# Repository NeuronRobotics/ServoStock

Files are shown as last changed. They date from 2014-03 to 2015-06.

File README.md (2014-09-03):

ServoStock
==========

This is the repository for the bowler enabled, closed loop controlled 3d printer. This repository is for all of the code for the printer.

# Control Application

From Eclipse for Java

* https://github.com/NeuronRobotics/java-bowler
* https://github.com/NeuronRobotics/NrConsole
* Jmonkey Game Engine

# Dependancies

## Compiler and c-bowler
Clone the c-bowler repository and install the compilers from here:

* https://github.com/NeuronRobotics/c-bowler

##MPLabx

Install MPLABX from here:

http://www.microchip.com/pagehandler/en-us/family/mplabx/

# Opening projects

Both repositoried should be in the same folder on your disk.

Open c-bowler in MPLABX

```
c-bowler/firmware/library/NR-Clib/development/c-bowler.X
```

And the ServoStock Code

```
ServoStock/firmware/MplabX_Projects/ServoPrinterController.X
```

You are ready to build and program.

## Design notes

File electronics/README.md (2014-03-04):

These are the assembly instructions for the ServoStock Electronics platform

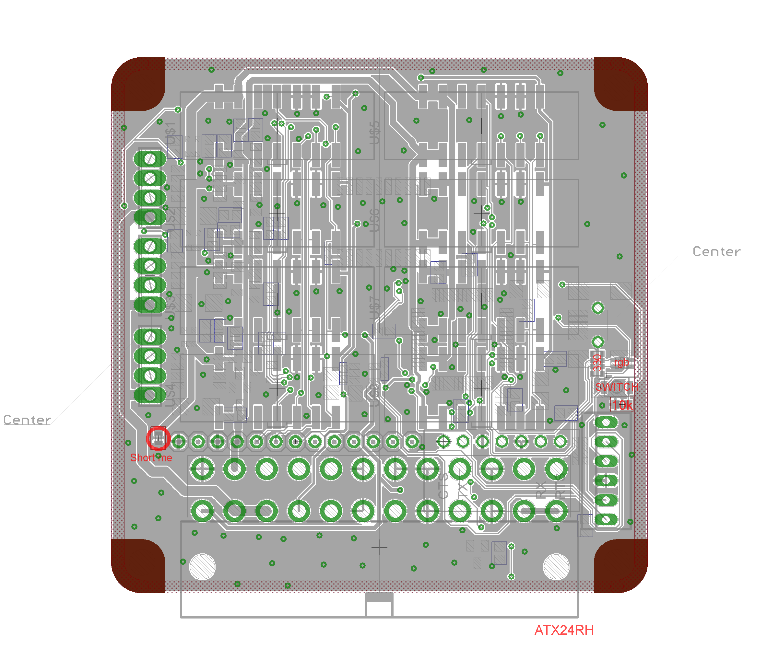
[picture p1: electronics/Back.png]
Top Components

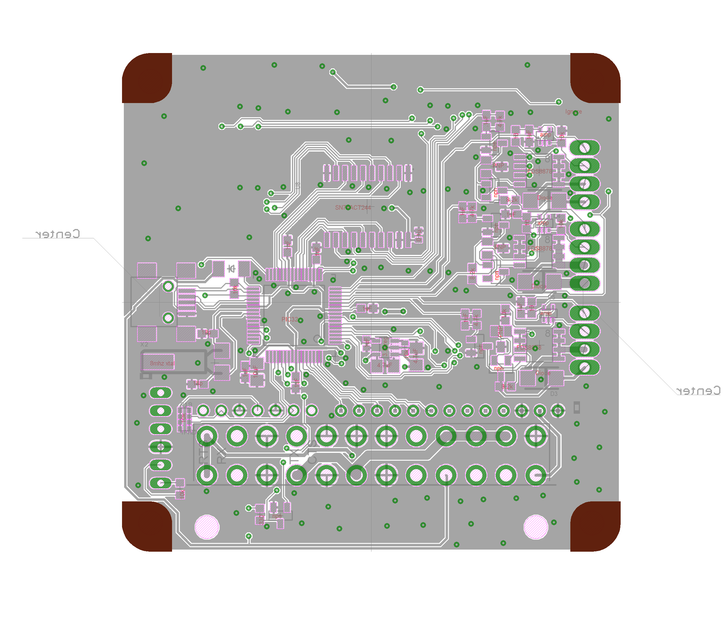
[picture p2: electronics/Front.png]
Bottom Components


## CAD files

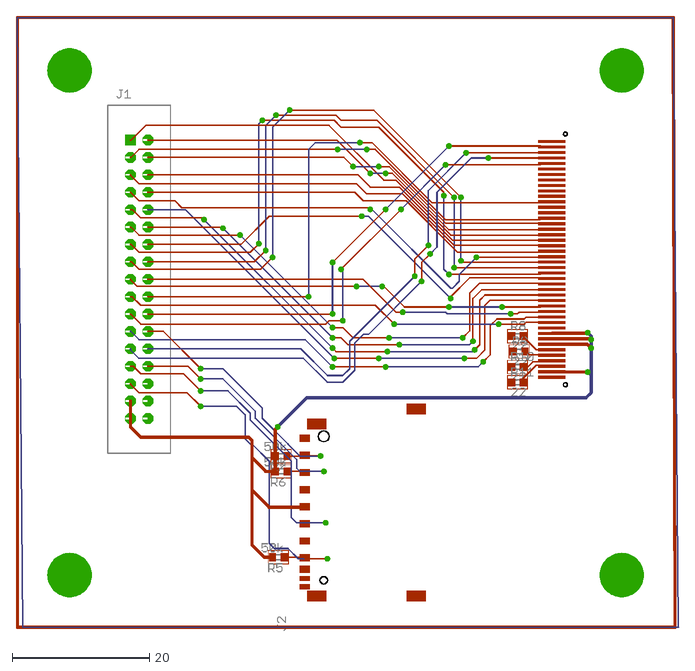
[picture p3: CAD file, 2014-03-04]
electronics/ReplicatorElectronics/lcd_brd/lcd_brd.dxf
96.8 x 89.7

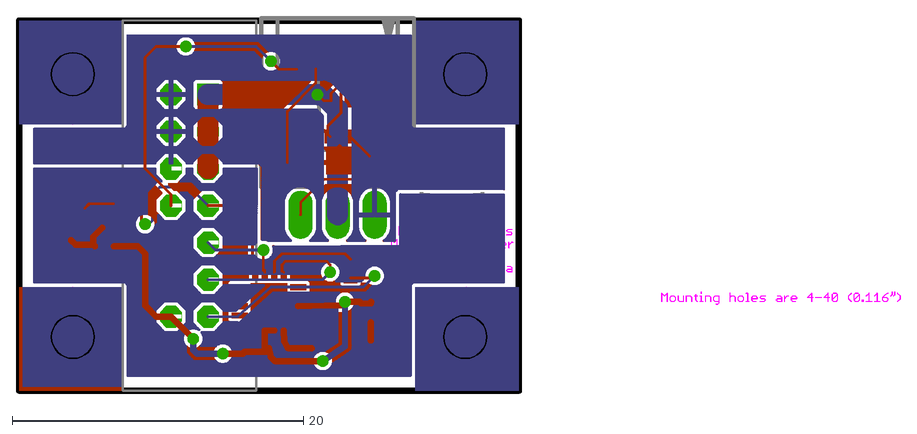
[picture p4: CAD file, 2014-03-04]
electronics/ReplicatorElectronics/magencoder/MagEnc2.dxf
60.7 x 25.9

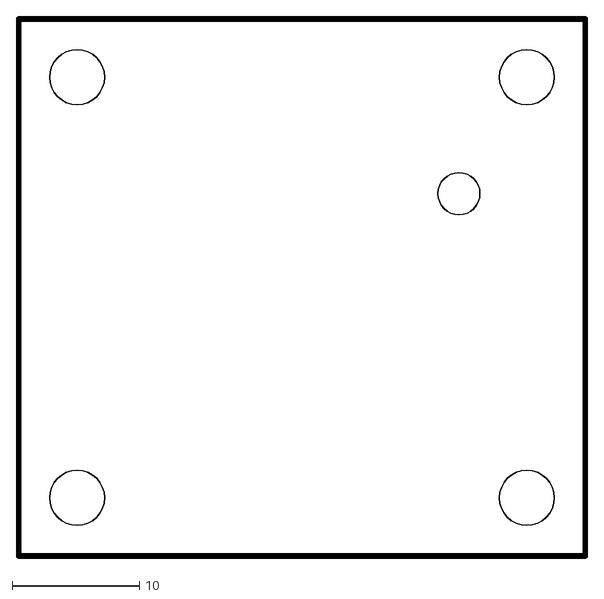
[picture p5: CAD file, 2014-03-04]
electronics/ReplicatorElectronics/temp_control/temp_control_holes.dxf
44.9 x 42.6

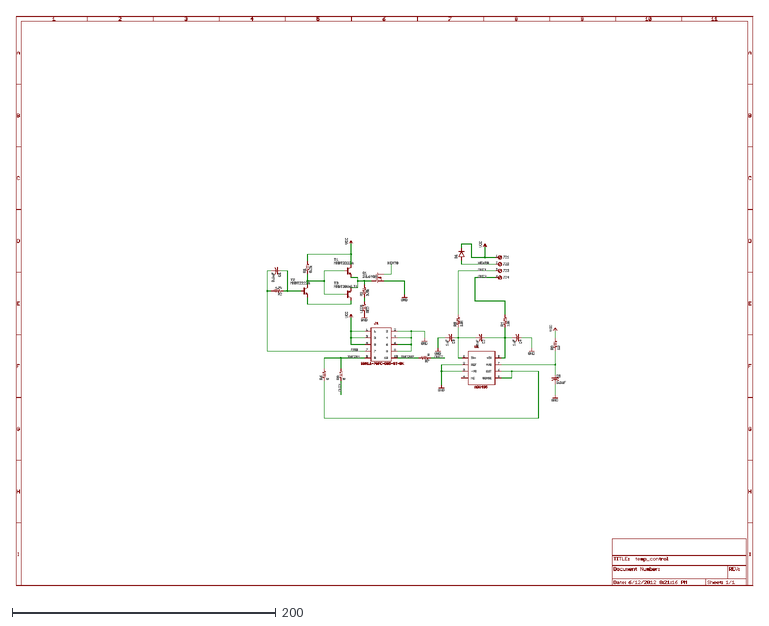
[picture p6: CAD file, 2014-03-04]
electronics/ReplicatorElectronics/temp_control/temp_control.dxf
559.1 x 432.1

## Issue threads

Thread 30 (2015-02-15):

Make a test Jig for an axis

acamilo, 2015-02-15:
Test jig needs to contain an aligned encoder board, motor, and magnet and needs to not become a part of another robot.

madhephaestus, 2015-02-16:
The spring-pin board needs to be created so these can be checked as fast as checking the dyio. Once the spring pin board is created, assign it to kent to build the jig.

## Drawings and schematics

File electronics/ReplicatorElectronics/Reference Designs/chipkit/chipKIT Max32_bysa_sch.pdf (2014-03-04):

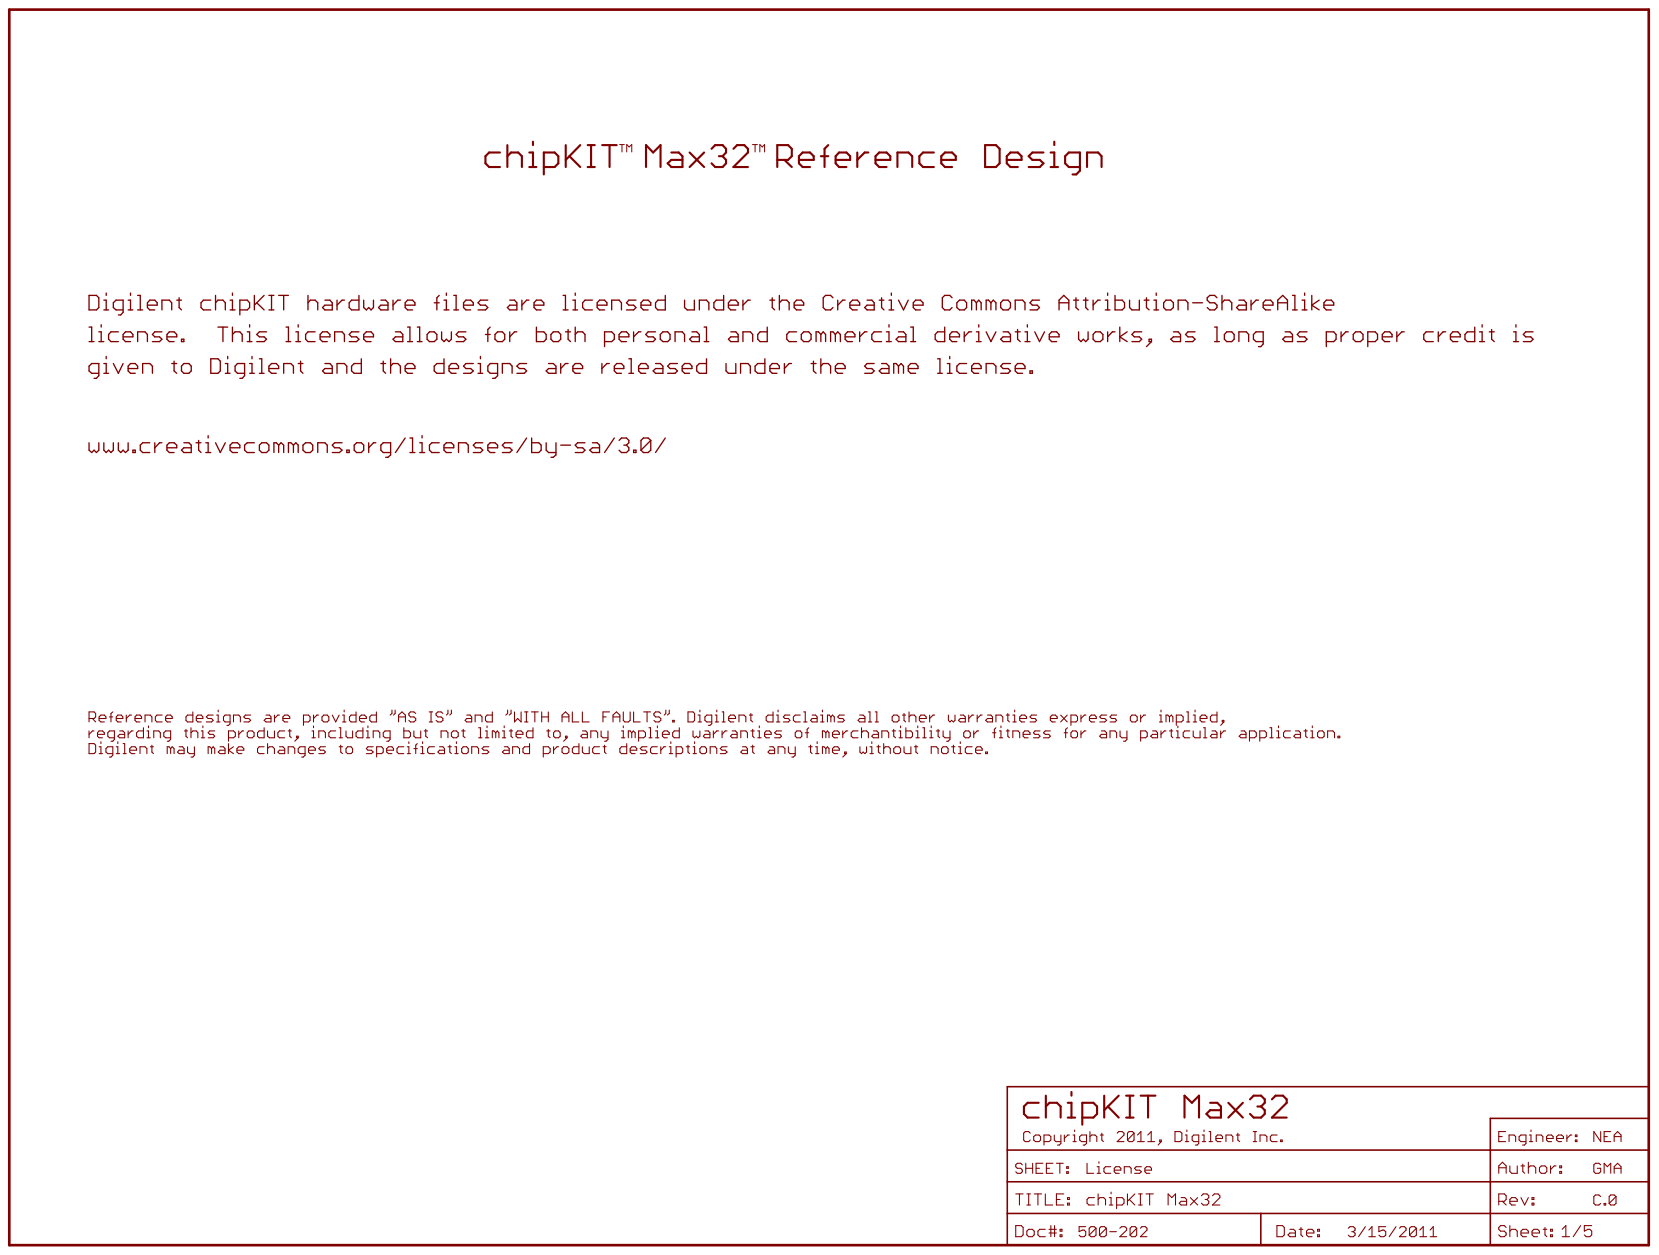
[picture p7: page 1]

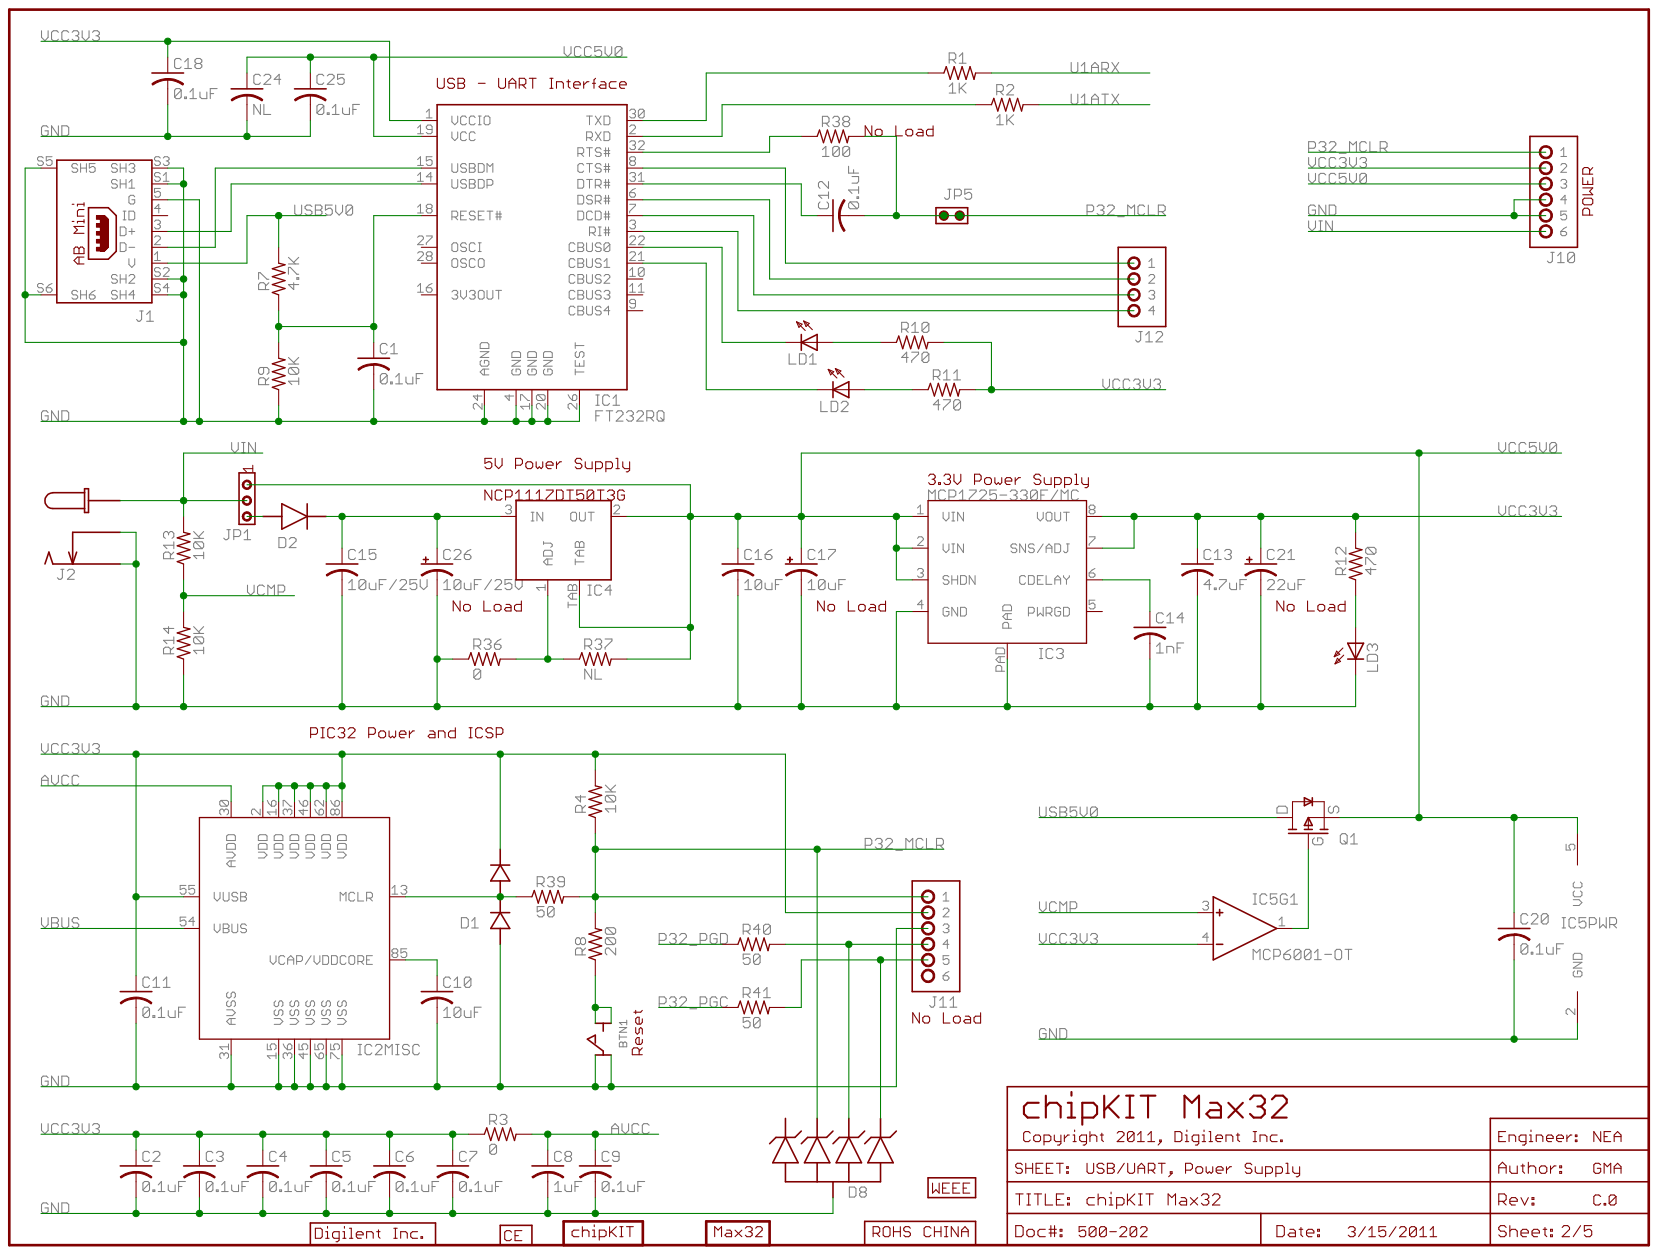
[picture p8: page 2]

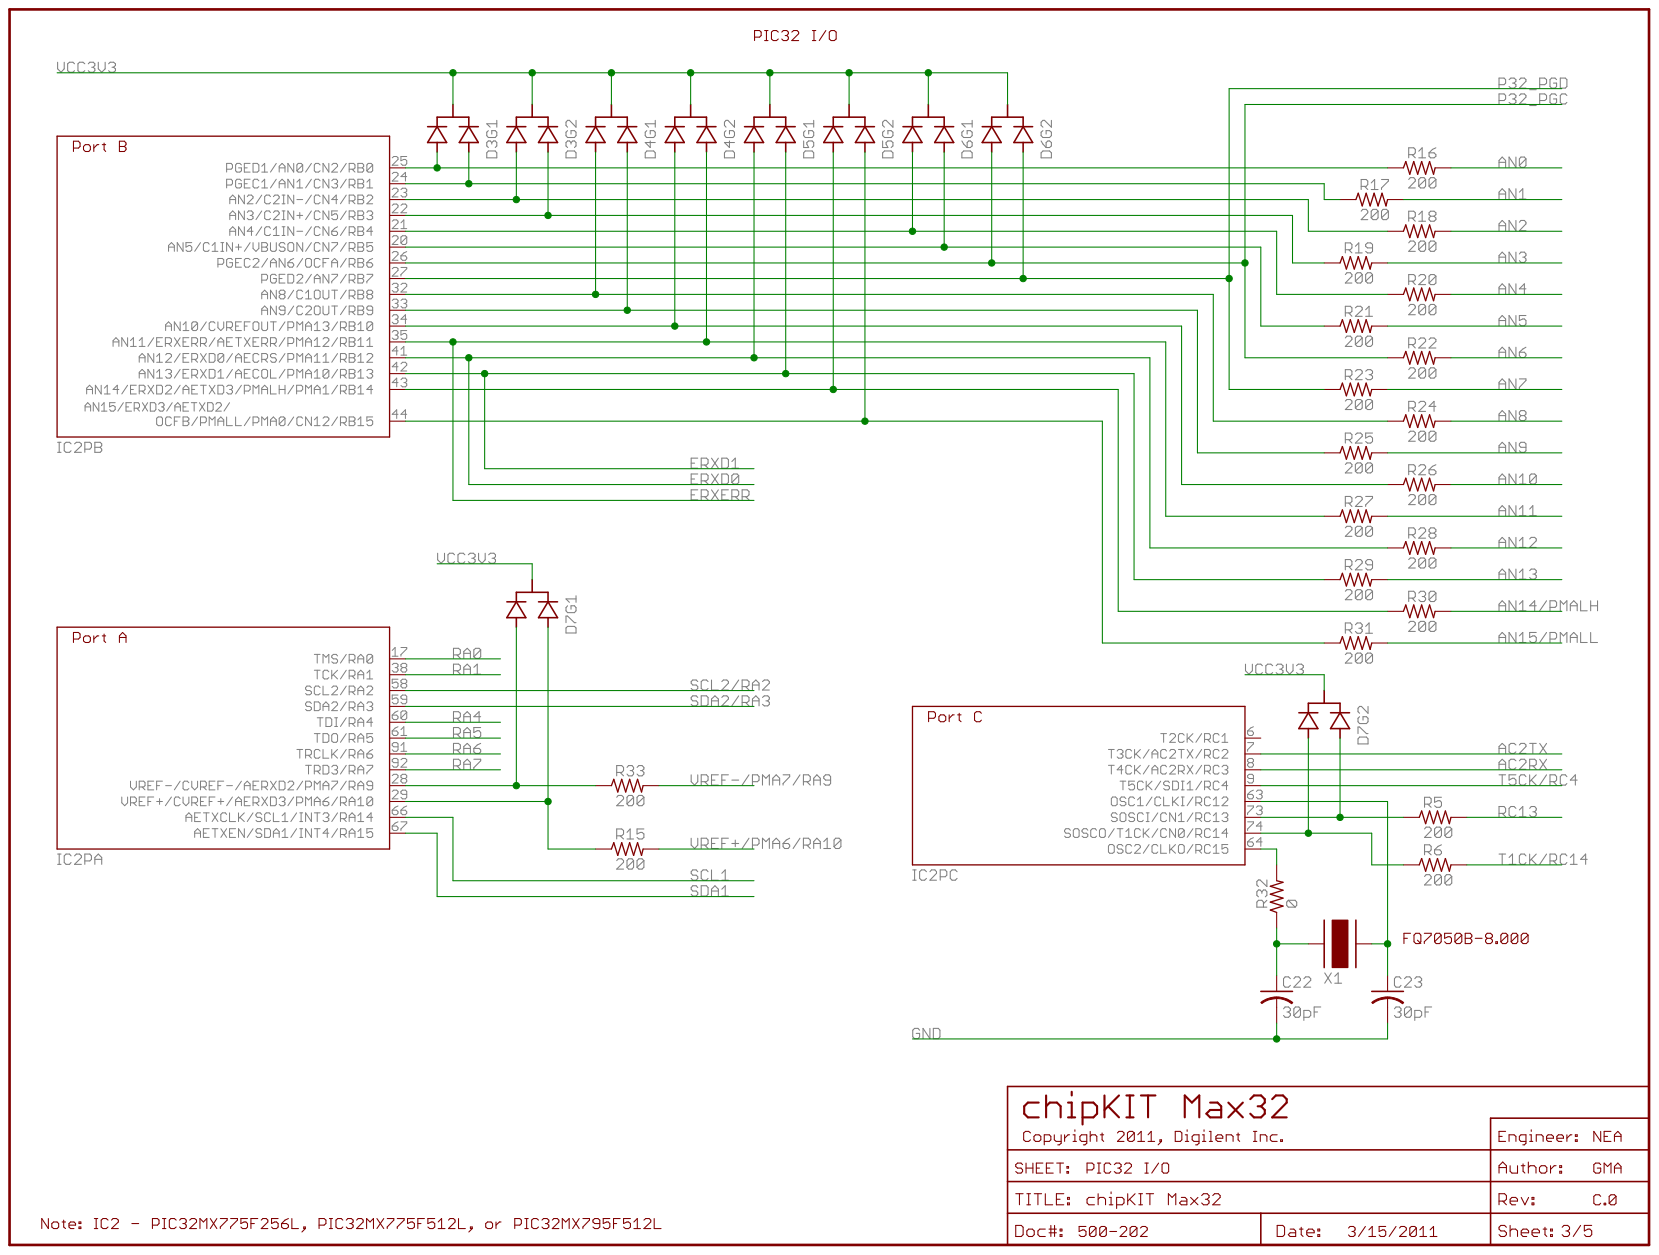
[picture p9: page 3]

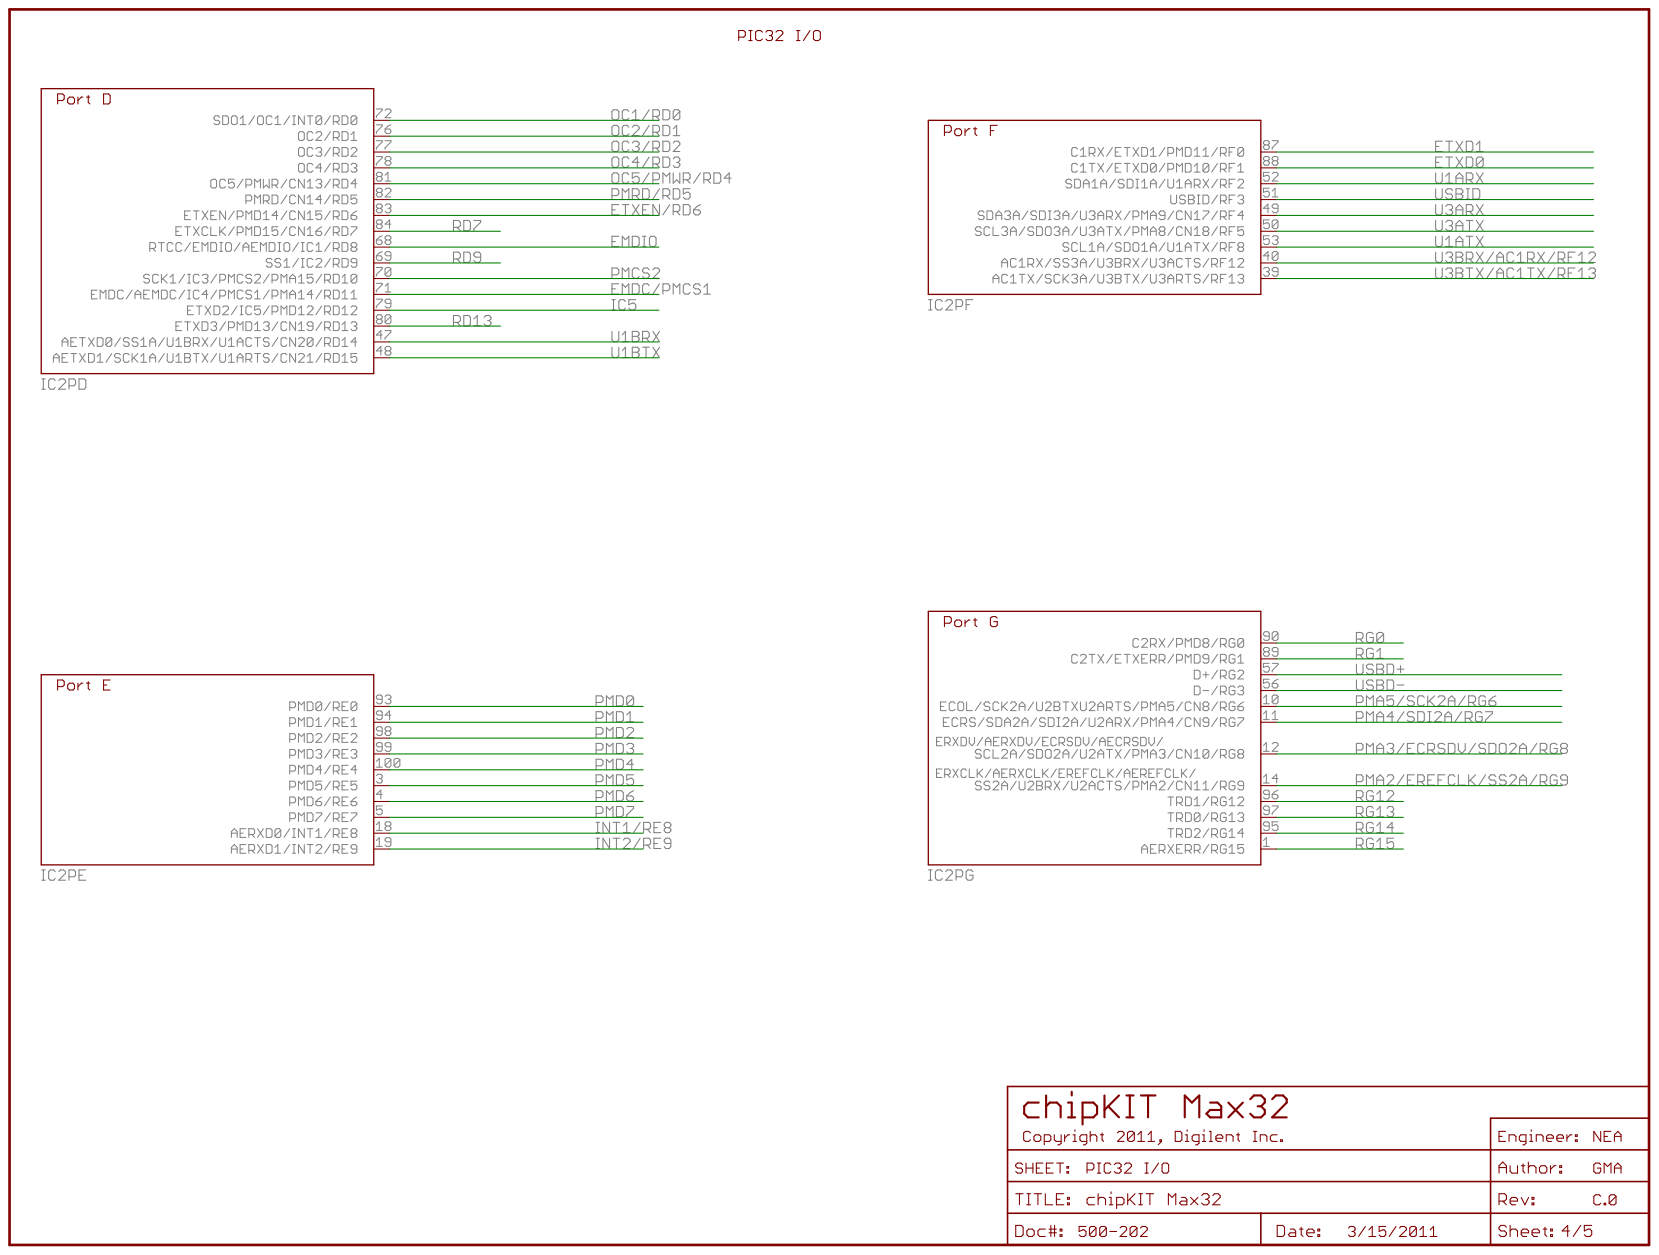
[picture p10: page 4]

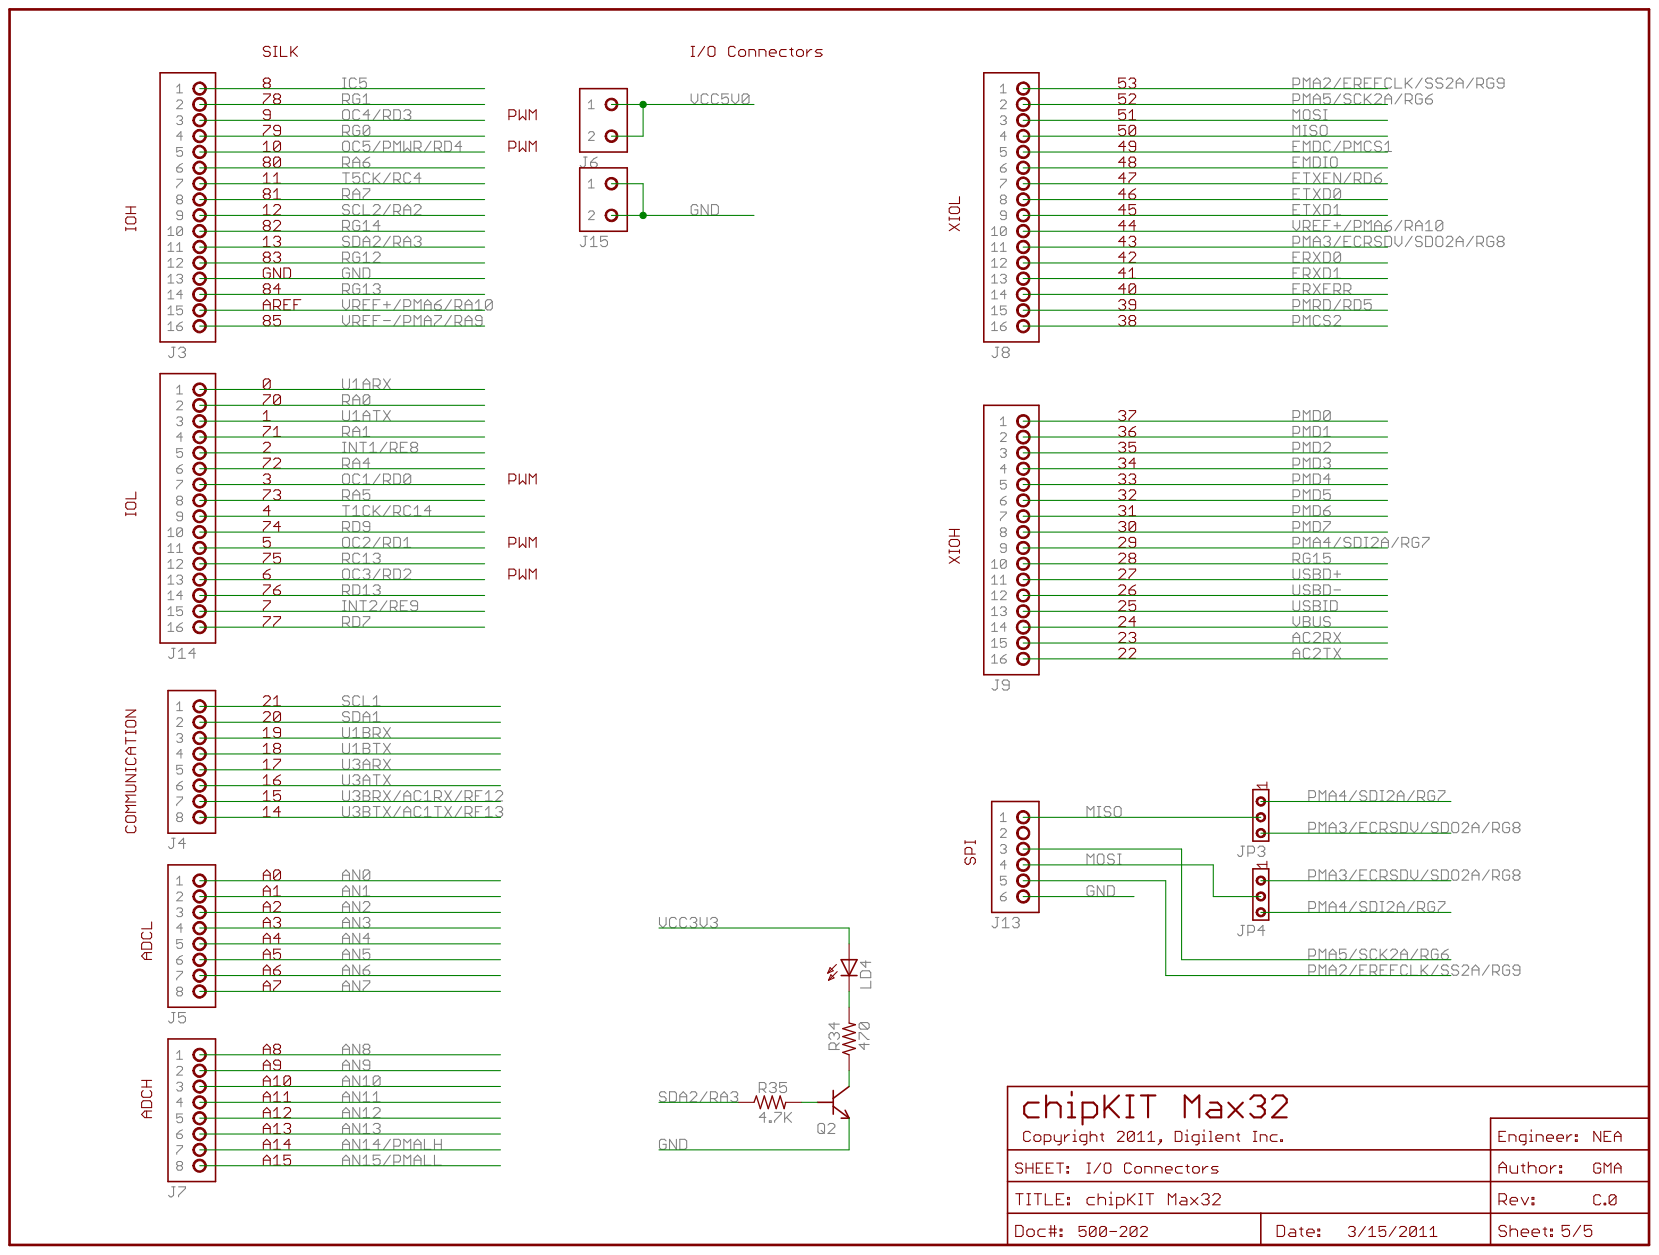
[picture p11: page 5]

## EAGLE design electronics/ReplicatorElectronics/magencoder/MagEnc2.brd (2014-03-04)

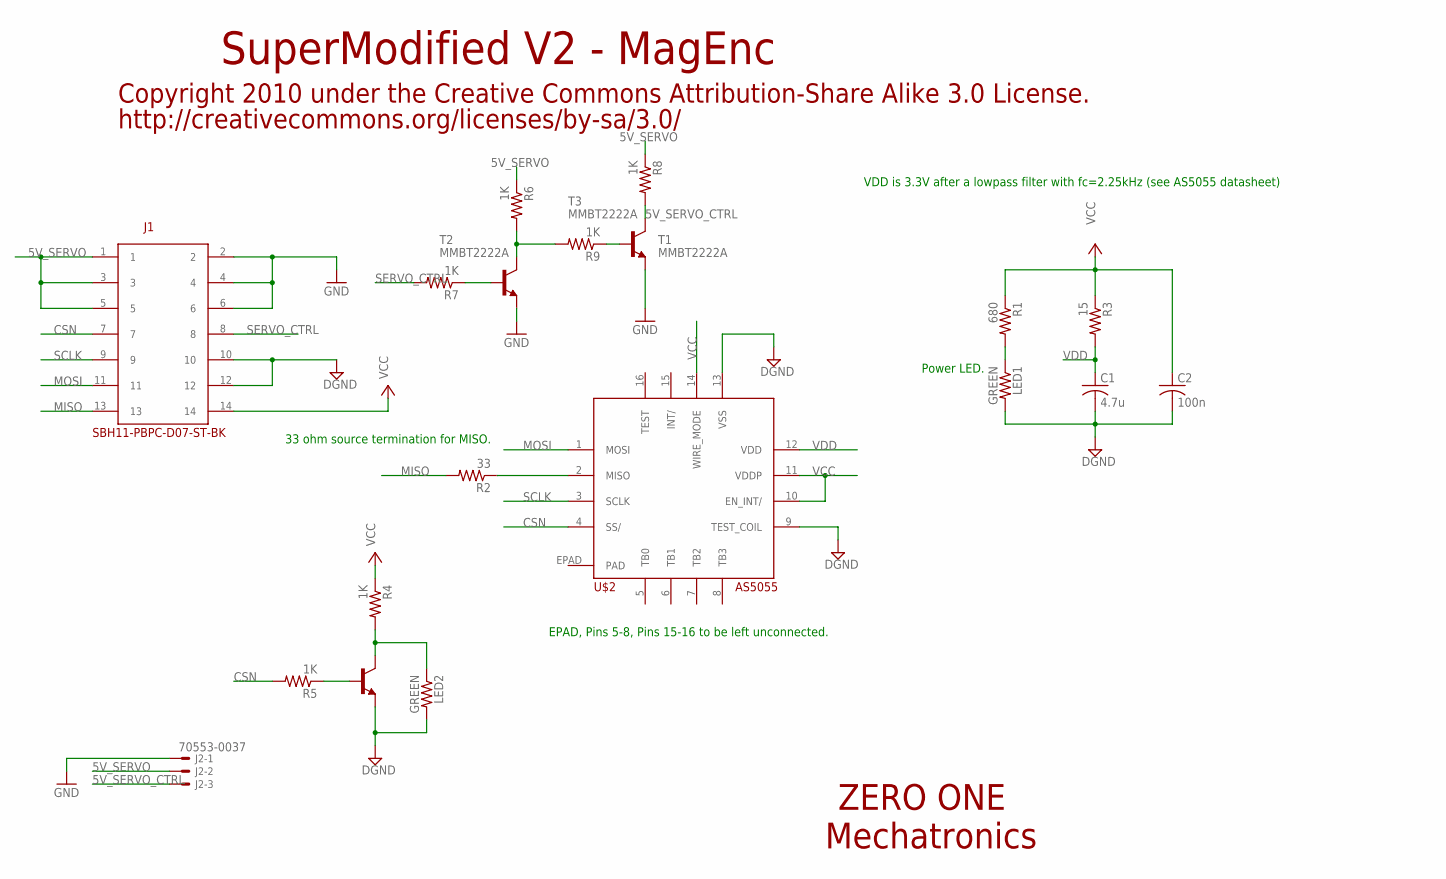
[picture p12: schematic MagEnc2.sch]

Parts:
C1: 4.7u; C0402
C2: 100n; C0402
J1: SBH11-PBPC-D07-ST-BK
J2: 70553-0037; 70553-03
LED1, LED2: GREEN; R0402
R1: 680; R0402
R2: 33; R0402
R3: 15; R0402
R4, R5, R6, R7, R8, R9: 1K; R0402
T1, T2, T3: MMBT2222A; SOT23-BEC
U$2: AS5055

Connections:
5V_SERVO: J1.1, J1.3, J1.5, J2.2, R6.1, R8.1
5V_SERVO_CTRL: J2.3, R8.2, T3.C
CSN: J1.7, R5.2, U$2.4 (SS/)
CSN1: R6.2, R9.2, T2.C
DGND: C1.2, C2.2, J1.10, J1.12, LED1.2, LED2.2, T1.E, U$2.9 (TEST_COIL), U$2.13 (VSS)
GND: J1.2, J1.4, J1.6, J2.1, T2.E, T3.E
MISO: J1.13, R2.2
MOSI: J1.11, U$2.1 (MOSI)
unnamed: LED1.1, R1.2
unnamed: LED2.1, R4.2, T1.C
unnamed: R5.1, T1.B
unnamed: R2.1, U$2.2 (MISO)
unnamed: R7.1, T2.B
unnamed: R9.1, T3.B
SCLK: J1.9, U$2.3 (SCLK)
SERVO_CTRL: J1.8, R7.2
VCC: C2.1, J1.14, R1.1, R3.1, R4.1, U$2.10 (EN_INT/), U$2.11 (VDDP), U$2.14 (WIRE_MODE)
VDD: C1.1, R3.2, U$2.12 (VDD)

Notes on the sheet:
ZERO ONE
Mechatronics
SuperModified V2 - MagEnc
Copyright 2010 under the Creative Commons Attribution-Share Alike 3.0 License.
http://creativecommons.org/licenses/by-sa/3.0/
VDD is 3.3V after a lowpass filter with fc=2.25kHz (see AS5055 datasheet)
EPAD, Pins 5-8, Pins 15-16 to be left unconnected.
33 ohm source termination for MISO.
Power LED.

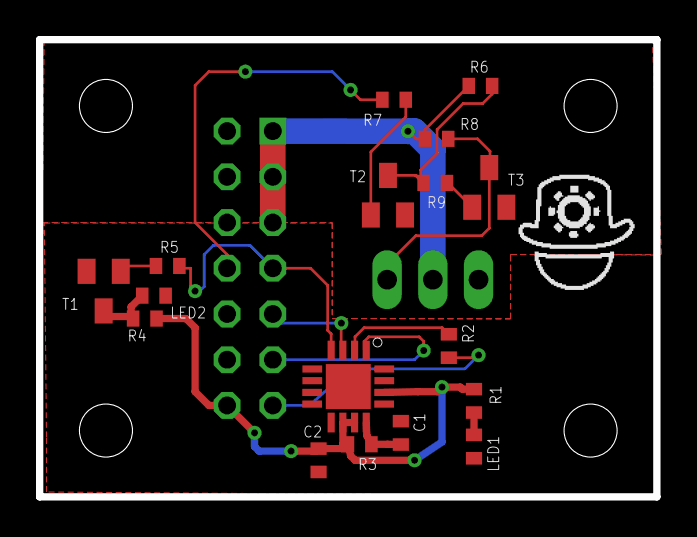
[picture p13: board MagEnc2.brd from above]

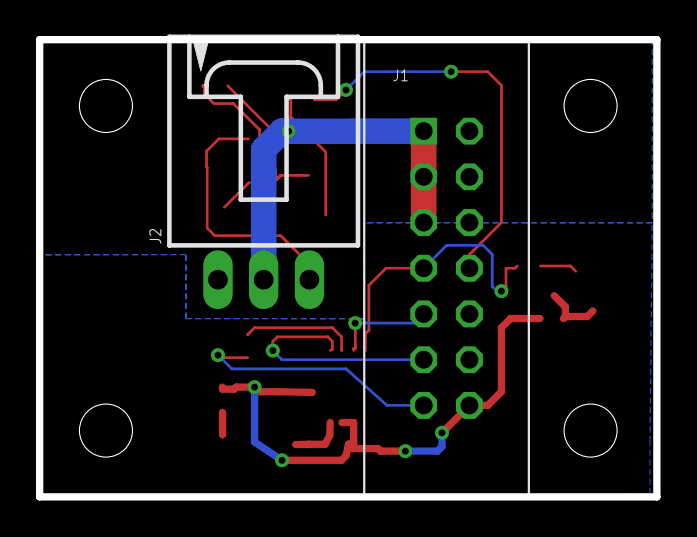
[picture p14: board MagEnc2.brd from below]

Board: 2 copper layers, 34.3 x 25.4 mm, 19 parts (2 on the bottom side), 18 nets.

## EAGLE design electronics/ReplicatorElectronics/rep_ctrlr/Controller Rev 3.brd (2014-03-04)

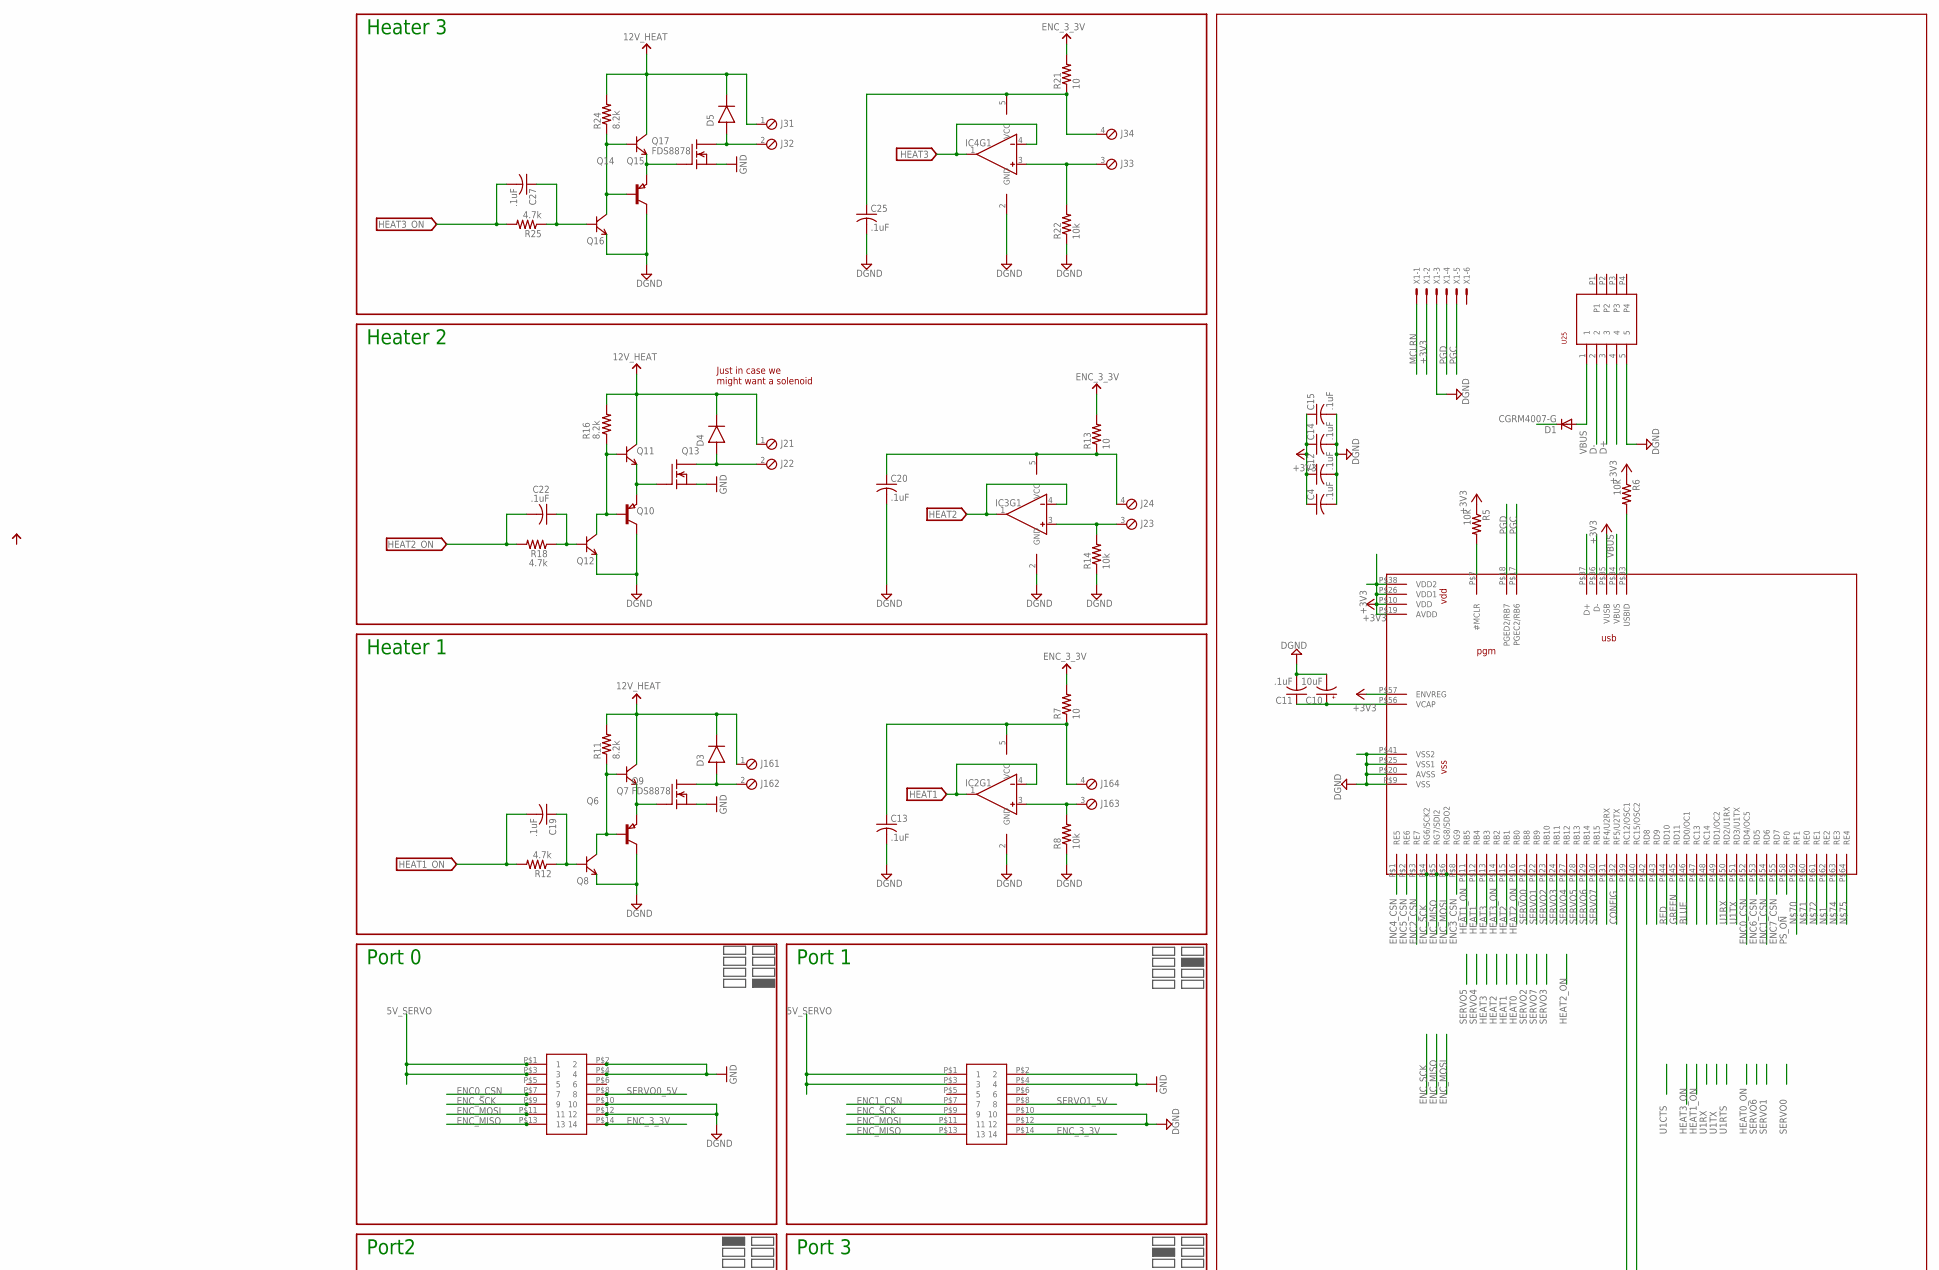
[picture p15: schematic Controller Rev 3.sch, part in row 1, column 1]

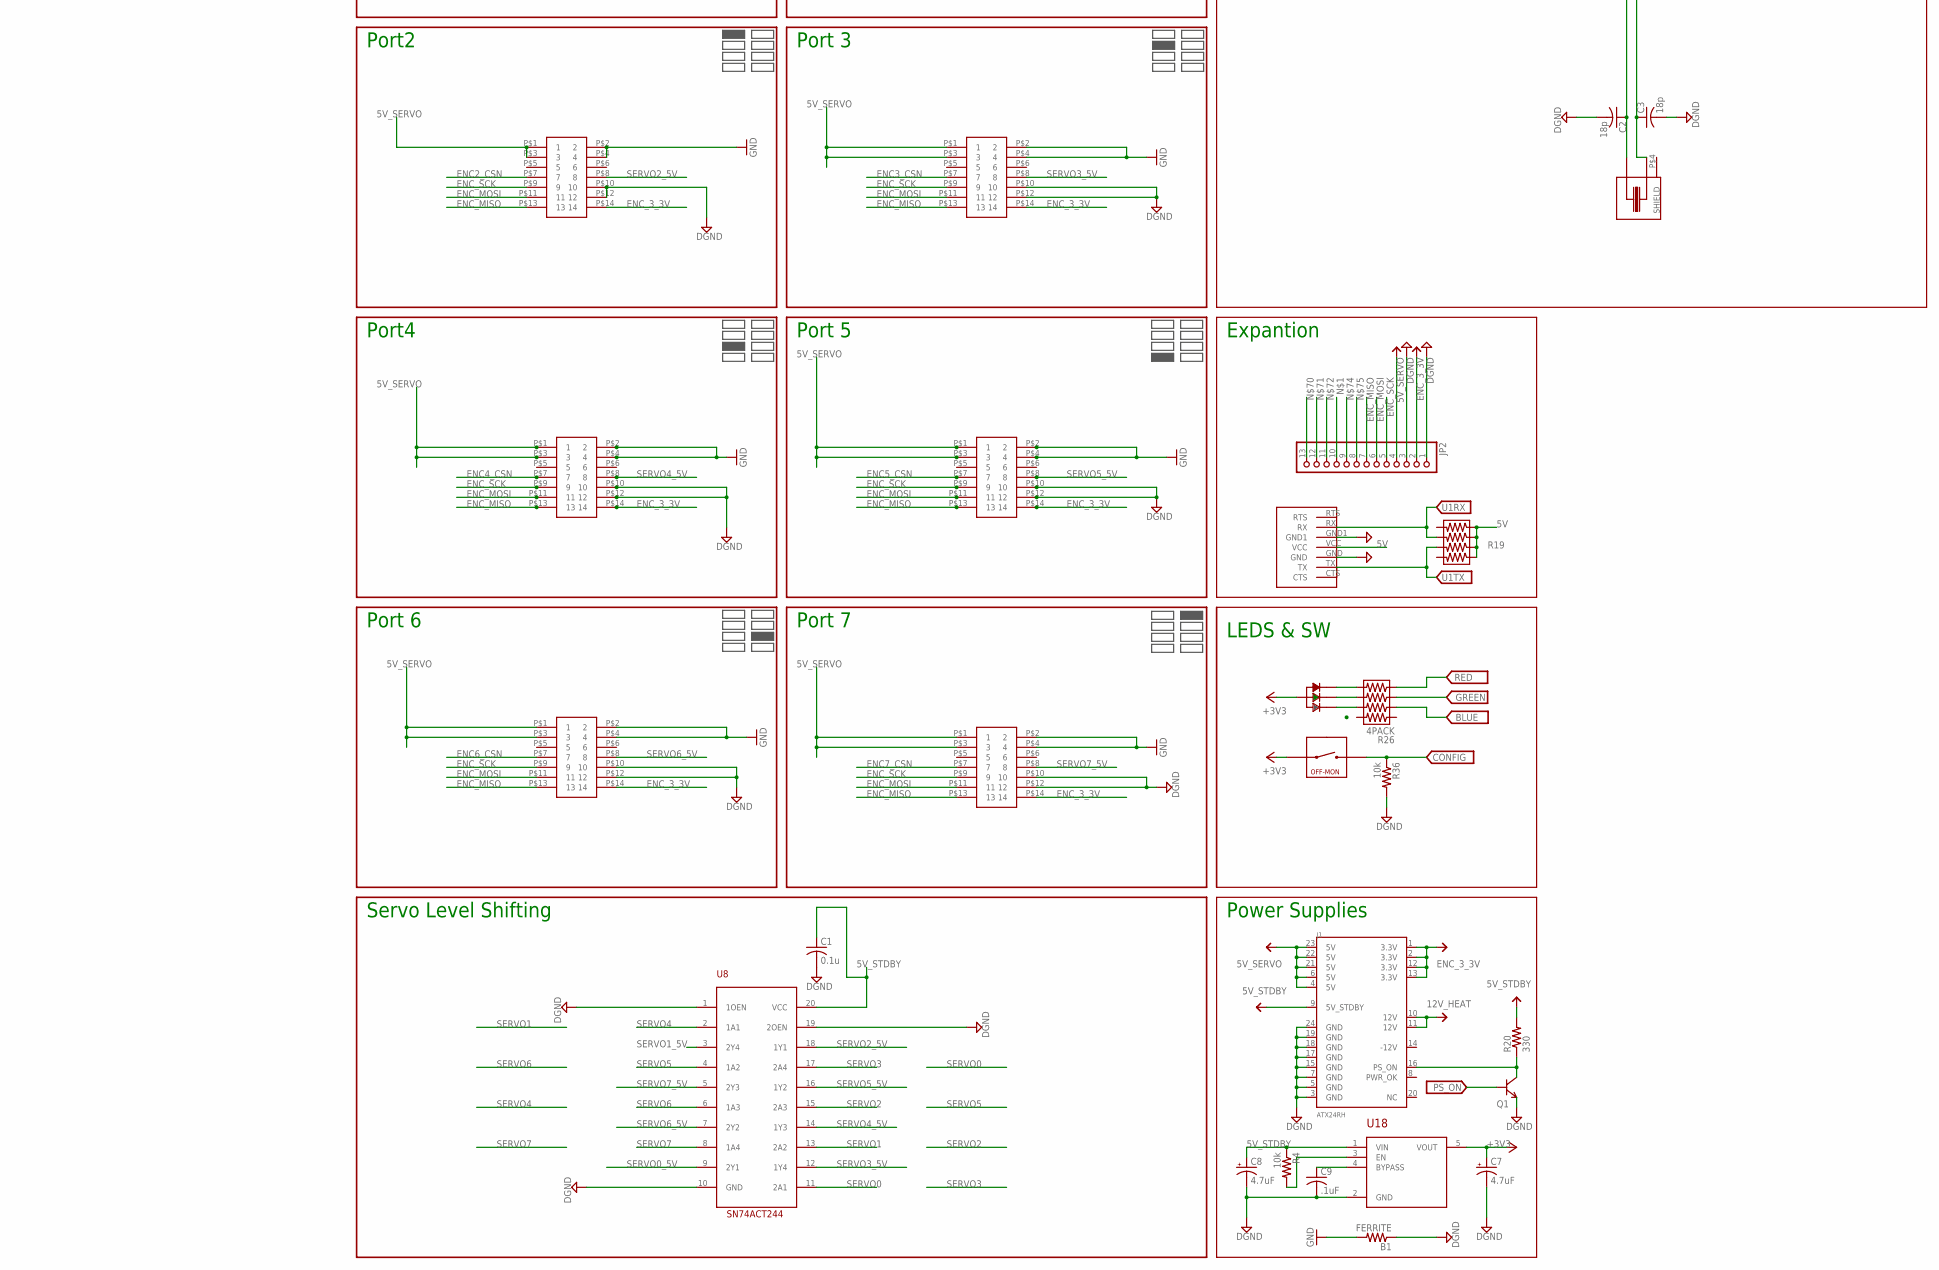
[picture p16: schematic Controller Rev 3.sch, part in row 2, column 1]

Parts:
B1: FERRITE; R0603
C1: 0.1u; C0402
C2, C3: 18p; C0603
C4, C11, C12, C13, C14, C15, C19, C20, C22, C25, C27: .1uF; C0603
C7, C8: 4.7uF; R/2012-12R
C9: .1uF; C0402
C10: 10uF; R/2012-12R
D1: CGRM4007-G; SOD-123_MINI-SMA
D3, D4, D5: DISCRETE_DIODESMA; DISCRETE_SMA
IC2, IC3, IC4: MICROCHIP_MCP6001-LT; MICROCHIP_SC70-5-LT
J1: ATX24RH; ATX24_RIGHT_ANGLE
J2, J3, J16: OSTVN04A150; 4POL254
J10: WASP7PIN
JP2: PINHD-1X13_BIG; 1X13-BIG
Q1, Q7, Q8, Q11, Q12, Q15, Q16: DISCRETE_MMBT3904LT1G; DISCRETE_SOT23
Q6, Q10, Q14: PNP-TRANSISTOR_SOT23; SOT23
Q9, Q13, Q17: FDS8878; SO-8
R4: 10k; R0402
R5, R6, R8, R14, R22, R36: 10k; R0603
R7, R13, R21: 10; R0603
R11, R16, R24: 8.2k; R0603
R12, R18, R25: 4.7k; R0603
R19, R26: 4PACK; 4PACK_0603
R20: 330; R0603
SW3: SPST; B3U-1000P
U1: TRI-LED-SMD; TRI_LED_SMD
U3: PIC32-64TQFP64-2; TQFP64-2
U8: SN74ACT244; 20-SOIC
U18: LDS3985XX33; SOT23-5
U25: 1734035-1_USB; 1734035-1_1734035
U$1, U$2, U$3, U$4, U$5, U$6, U$7, U$8: SBH11-NBPC-D07-SM-BK
X1: 22-23-2061
X2: CMR3XXT; CMR309T

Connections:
5V: J10.VCC, R19.R1B, R19.R2B, R19.R3B, R19.R4B
5V_SERVO: J1.4 (5V), J1.6 (5V), J1.21 (5V), J1.22 (5V), J1.23 (5V), JP2.4, U$1.P$1 (1), U$1.P$3 (3), U$2.P$1 (1), U$2.P$3 (3), U$3.P$1 (1), U$3.P$3 (3), U$4.P$1 (1), U$4.P$3 (3), U$5.P$1 (1), U$5.P$3 (3), U$6.P$1 (1), U$6.P$3 (3), U$7.P$1 (1), U$7.P$3 (3), U$8.P$1 (1), U$8.P$3 (3)
5V_STDBY: C1.1, C8.+, D1.C, J1.9 (5V_STDBY), R4.1, R20.2, U8.20 (VCC), U18.1 (VIN)
12V_HEAT: D3.C, D4.C, D5.C, J1.10 (12V), J1.11 (12V), J2.1, J3.1, J16.1, Q7.3 (C), Q11.3 (C), Q15.3 (C), R11.2, R16.2, R24.2
12V_SW1: D3.A, J16.2, Q9.5 (D), Q9.6 (D), Q9.7 (D), Q9.8 (D)
12V_SW2: D4.A, J2.2, Q13.5 (D), Q13.6 (D), Q13.7 (D), Q13.8 (D)
12V_SW3: D5.A, J3.2, Q17.5 (D), Q17.6 (D), Q17.7 (D), Q17.8 (D)
+3V3: C4.1, C7.+, C12.1, C14.1, C15.1, R5.1, R6.1, SW3.P$1, U1.COMM-A, U3.P$10 (VDD), U3.P$19 (AVDD), U3.P$26 (VDD1), U3.P$35 (VUSB), U3.P$38 (VDD2), U3.P$57 (ENVREG), U18.5 (VOUT), X1.2
B: R26.R2A, U1.BLUE
BLUE: R26.R2B, U3.P$46 (RD0/OC1)
CONFIG: R36.1, SW3.P$3, U3.P$32 (RF5/U2TX)
D+: U3.P$37 (D+), U25.3
D-: U3.P$36 (D-), U25.2
DGND: B1.1, C1.2, C2.2, C3.2, C4.2, C7.-, C8.-, C9.2, C10.-, C11.2, C12.2, C13.2, C14.2, C15.2, C20.2, C25.2, IC2.2 (GND), IC3.2 (GND), IC4.2 (GND), J1.3 (GND), J1.5 (GND), J1.7 (GND), J1.15 (GND), J1.17 (GND), J1.18 (GND), J1.19 (GND), J1.24 (GND), J10.GND, J10.GND1, JP2.1, JP2.3, Q1.2 (E), Q6.3 (C), Q8.2 (E), Q10.3 (C), Q12.2 (E), Q14.3 (C), Q16.2 (E), R8.1, R14.1, R22.1, R36.2, U3.P$9 (VSS), U3.P$20 (AVSS), U3.P$25 (VSS1), U3.P$41 (VSS2), U8.1 (1OEN), U8.10 (GND), U8.19 (2OEN), U18.2 (GND), U25.5, U$1.P$10 (10), U$1.P$12 (12), U$2.P$10 (10), U$2.P$12 (12), U$3.P$10 (10), U$3.P$12 (12), U$4.P$10 (10), U$4.P$12 (12), U$5.P$10 (10), U$5.P$12 (12), U$6.P$10 (10), U$6.P$12 (12), U$7.P$10 (10), U$7.P$12 (12), U$8.P$10 (10), U$8.P$12 (12), X1.3
ENC0_CSN: U3.P$52 (RD4/OC5), U$8.P$7 (7)
ENC1_CSN: U3.P$54 (RD6), U$6.P$7 (7)
ENC2_CSN: U3.P$3 (RE7), U$1.P$7 (7)
ENC3_CSN: U3.P$8 (RG9), U$2.P$7 (7)
ENC4_CSN: U3.P$1 (RE5), U$3.P$7 (7)
ENC5_CSN: U3.P$2 (RE6), U$4.P$7 (7)
ENC6_CSN: U3.P$53 (RD5), U$7.P$7 (7)
ENC7_CSN: U3.P$55 (RD7), U$5.P$7 (7)
ENC_3_3V: J1.1 (3.3V), J1.2 (3.3V), J1.12 (3.3V), J1.13 (3.3V), JP2.2, R7.2, R13.2, R21.2, U$1.P$14 (14), U$2.P$14 (14), U$3.P$14 (14), U$4.P$14 (14), U$5.P$14 (14), U$6.P$14 (14), U$7.P$14 (14), U$8.P$14 (14)
ENC_MISO: JP2.7, U3.P$5 (RG7/SDI2), U$1.P$13 (13), U$2.P$13 (13), U$3.P$13 (13), U$4.P$13 (13), U$5.P$13 (13), U$6.P$13 (13), U$7.P$13 (13), U$8.P$13 (13)
ENC_MOSI: JP2.6, U3.P$6 (RG8/SDO2), U$1.P$11 (11), U$2.P$11 (11), U$3.P$11 (11), U$4.P$11 (11), U$5.P$11 (11), U$6.P$11 (11), U$7.P$11 (11), U$8.P$11 (11)
ENC_SCK: JP2.5, U3.P$4 (RG6/SCK2), U$1.P$9 (9), U$2.P$9 (9), U$3.P$9 (9), U$4.P$9 (9), U$5.P$9 (9), U$6.P$9 (9), U$7.P$9 (9), U$8.P$9 (9)
G: R26.R3A, U1.GRN
GND: B1.2, Q9.1 (S), Q9.2 (S), Q9.3 (S), Q13.1 (S), Q13.2 (S), Q13.3 (S), Q17.1 (S), Q17.2 (S), Q17.3 (S), U$1.P$2 (2), U$1.P$4 (4), U$2.P$2 (2), U$2.P$4 (4), U$3.P$2 (2), U$3.P$4 (4), U$4.P$2 (2), U$4.P$4 (4), U$5.P$2 (2), U$5.P$4 (4), U$6.P$2 (2), U$6.P$4 (4), U$7.P$2 (2), U$7.P$4 (4), U$8.P$2 (2), U$8.P$4 (4)
GREEN: R26.R3B, U3.P$45 (RD11)
HEAT1: IC2.1 (OUT), IC2.4 (IN-), U3.P$12 (RB4)
HEAT1_ON: C19.2, R12.2, U3.P$11 (RB5)
HEAT2: IC3.1 (OUT), IC3.4 (IN-), U3.P$15 (RB1)
HEAT2_ON: C22.2, R18.2, U3.P$16 (RB0)
HEAT3: IC4.1 (OUT), IC4.4 (IN-), U3.P$13 (RB3)
HEAT3_ON: C27.2, R25.2, U3.P$14 (RB2)
MCLRN: R5.2, U3.P$7 (#MCLR), X1.1
unnamed: JP2.10, U3.P$62 (RE2)
unnamed: R4.2, U18.3 (EN)
unnamed: C9.1, U18.4 (BYPASS)
unnamed: C3.1, U3.P$40 (RC15/OSC2), X2.P$3
unnamed: C10.+, C11.1, U3.P$56 (VCAP)
unnamed: C2.1, U3.P$39 (RC12/OSC1), X2.P$1
unnamed: IC2.3 (IN+), J16.3, R8.2
unnamed: C13.1, IC2.5 (VCC), J16.4, R7.1
unnamed: Q6.1 (B), Q7.1 (B), Q8.3 (C), R11.1
unnamed: C19.1, Q8.1 (B), R12.1
unnamed: Q6.2 (E), Q7.2 (E), Q9.4 (G)
unnamed: IC3.3 (IN+), J2.3, R14.2
unnamed: C20.1, IC3.5 (VCC), J2.4, R13.1
unnamed: Q10.1 (B), Q11.1 (B), Q12.3 (C), R16.1
unnamed: C22.1, Q12.1 (B), R18.1
unnamed: Q10.2 (E), Q11.2 (E), Q13.4 (G)
unnamed: IC4.3 (IN+), J3.3, R22.2
unnamed: C25.1, IC4.5 (VCC), J3.4, R21.1
unnamed: Q14.1 (B), Q15.1 (B), Q16.3 (C), R24.1
unnamed: C27.1, Q16.1 (B), R25.1
unnamed: Q14.2 (E), Q15.2 (E), Q17.4 (G)
unnamed: J1.16 (PS_ON), Q1.3 (C), R20.1
unnamed: JP2.13, U3.P$59 (RF1)
unnamed: JP2.12, U3.P$60 (RE0)
unnamed: JP2.11, U3.P$61 (RE1)
unnamed: JP2.9, U3.P$63 (RE3)
unnamed: JP2.8, U3.P$64 (RE4)
PGC: U3.P$17 (PGEC2/RB6), X1.5
PGD: U3.P$18 (PGED2/RB7), X1.4
PS_ON: Q1.1 (B), U3.P$58 (RF0)
R: R26.R4A, U1.RED
RED: R26.R4B, U3.P$44 (RD10)
SERVO0: U3.P$21 (RB8), U8.11 (2A1)
SERVO0_5V: U8.9 (2Y1), U$8.P$8 (8)
SERVO1: U3.P$22 (RB9), U8.13 (2A2)
SERVO1_5V: U8.3 (2Y4), U$6.P$8 (8)
SERVO2: U3.P$23 (RB10), U8.15 (2A3)
SERVO2_5V: U8.18 (1Y1), U$1.P$8 (8)
SERVO3: U3.P$24 (RB11), U8.17 (2A4)
SERVO3_5V: U8.12 (1Y4), U$2.P$8 (8)
SERVO4: U3.P$27 (RB12), U8.2 (1A1)
SERVO4_5V: U8.14 (1Y3), U$3.P$8 (8)
SERVO5: U3.P$28 (RB13), U8.4 (1A2)
SERVO5_5V: U8.16 (1Y2), U$4.P$8 (8)
SERVO6: U3.P$29 (RB14), U8.6 (1A3)
SERVO6_5V: U8.7 (2Y2), U$7.P$8 (8)
SERVO7: U3.P$30 (RB15), U8.8 (1A4)
SERVO7_5V: U8.5 (2Y3), U$5.P$8 (8)
U1RX: J10.RX, R19.R2A, U3.P$50 (RD2/U1RX)
U1TX: J10.TX, R19.R3A, U3.P$51 (RD3/U1TX)
USBID: R6.2, U3.P$33 (USBID), U25.4
VBUS: D1.A, U3.P$34 (VBUS), U25.1

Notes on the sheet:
Just in case we might want a solenoid
Heater 2
Heater 1
Heater 3
LEDS & SW
Power Supplies
Servo Level Shifting
Port 6
Port 7
Port 5
Port4
Port2
Port 3
Port 1
Port 0
Expantion

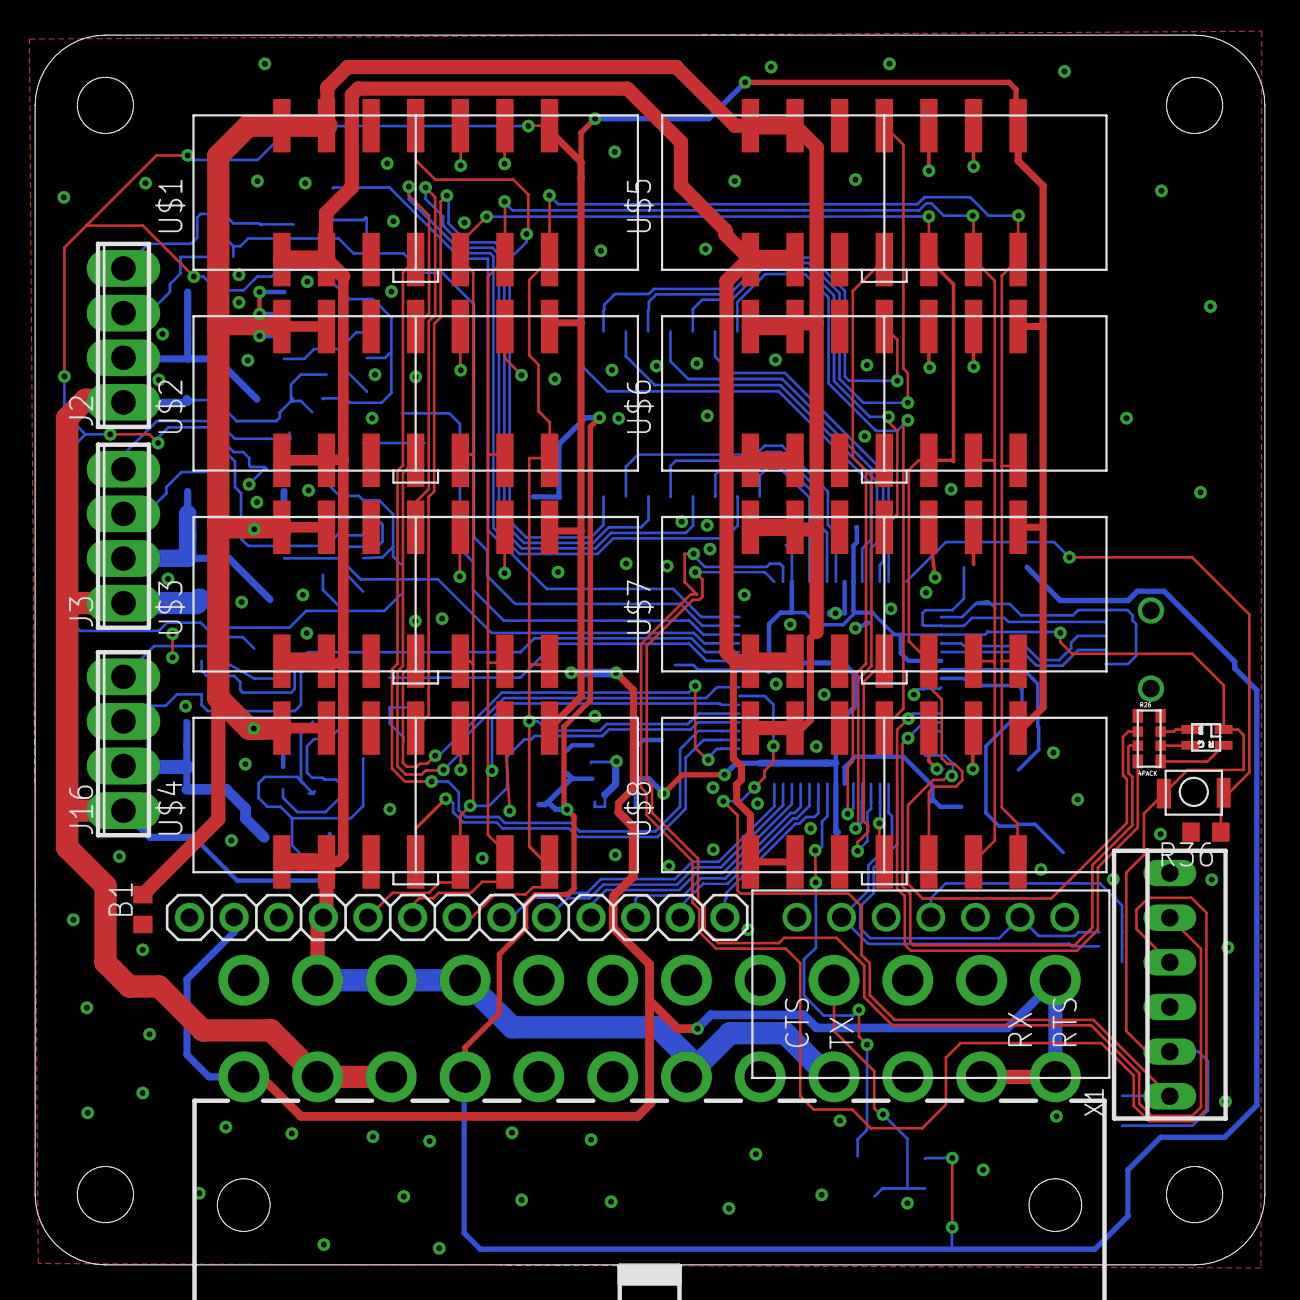
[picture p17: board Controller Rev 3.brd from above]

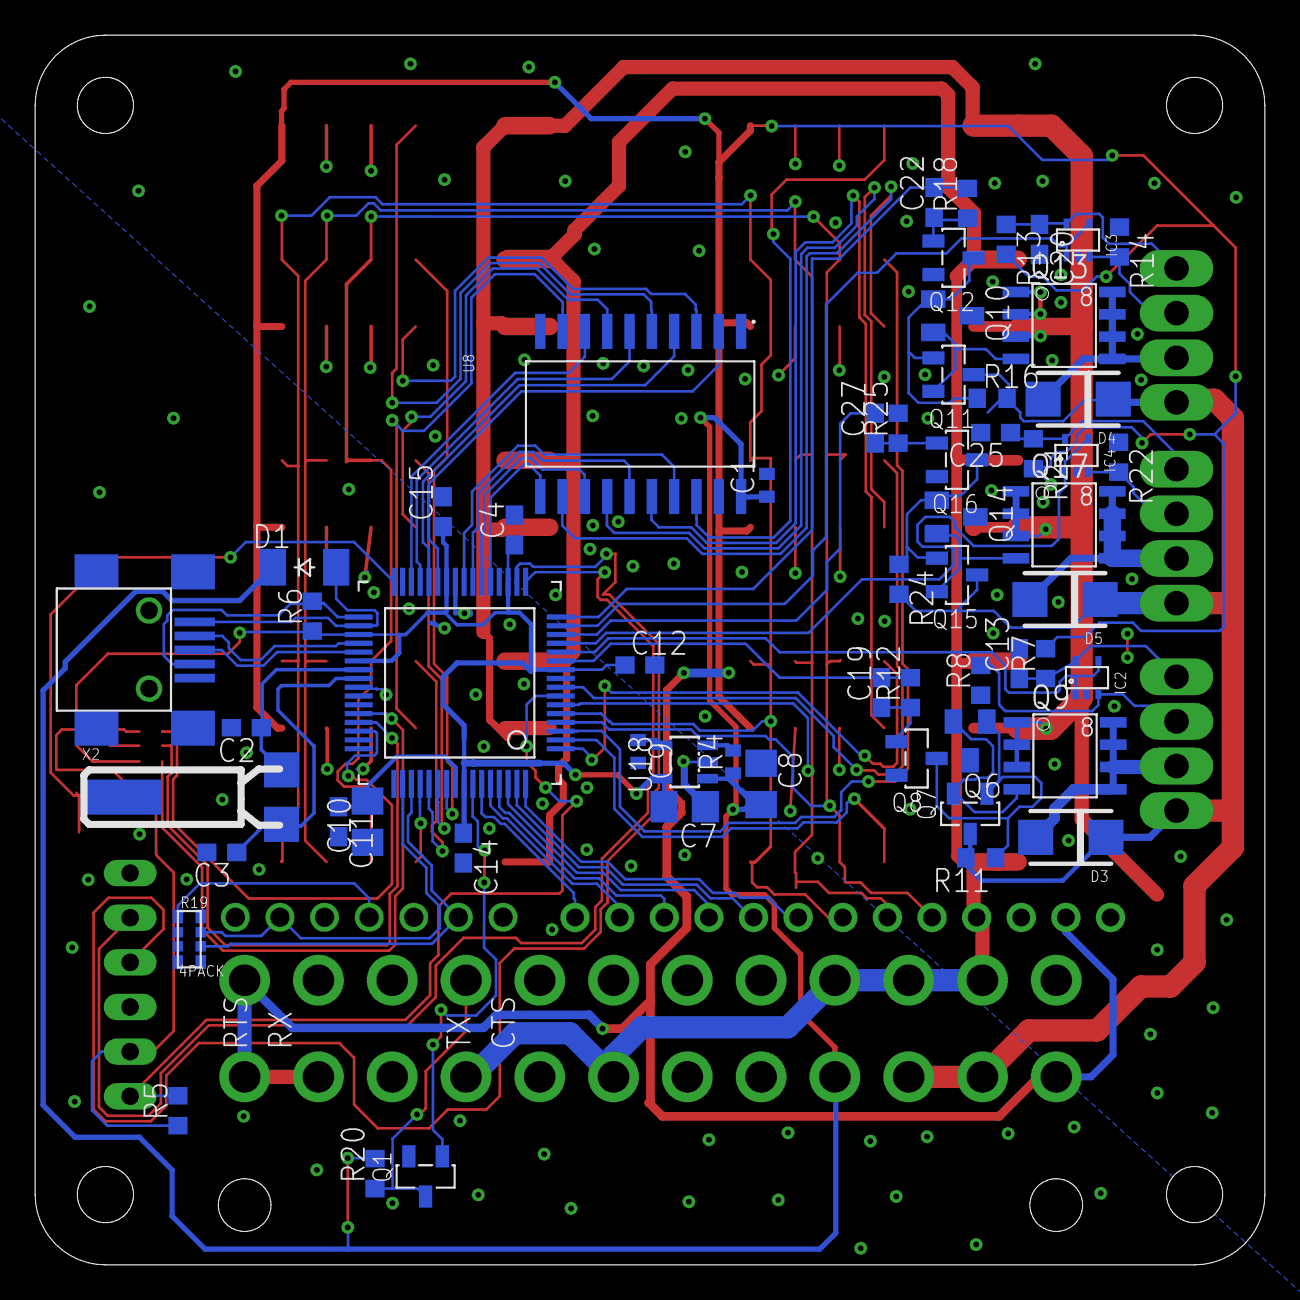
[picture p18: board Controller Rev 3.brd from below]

Board: 2 copper layers, 70.0 x 70.0 mm, 81 parts (60 on the bottom side), 88 nets.

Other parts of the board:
U$9: DP7070_V1

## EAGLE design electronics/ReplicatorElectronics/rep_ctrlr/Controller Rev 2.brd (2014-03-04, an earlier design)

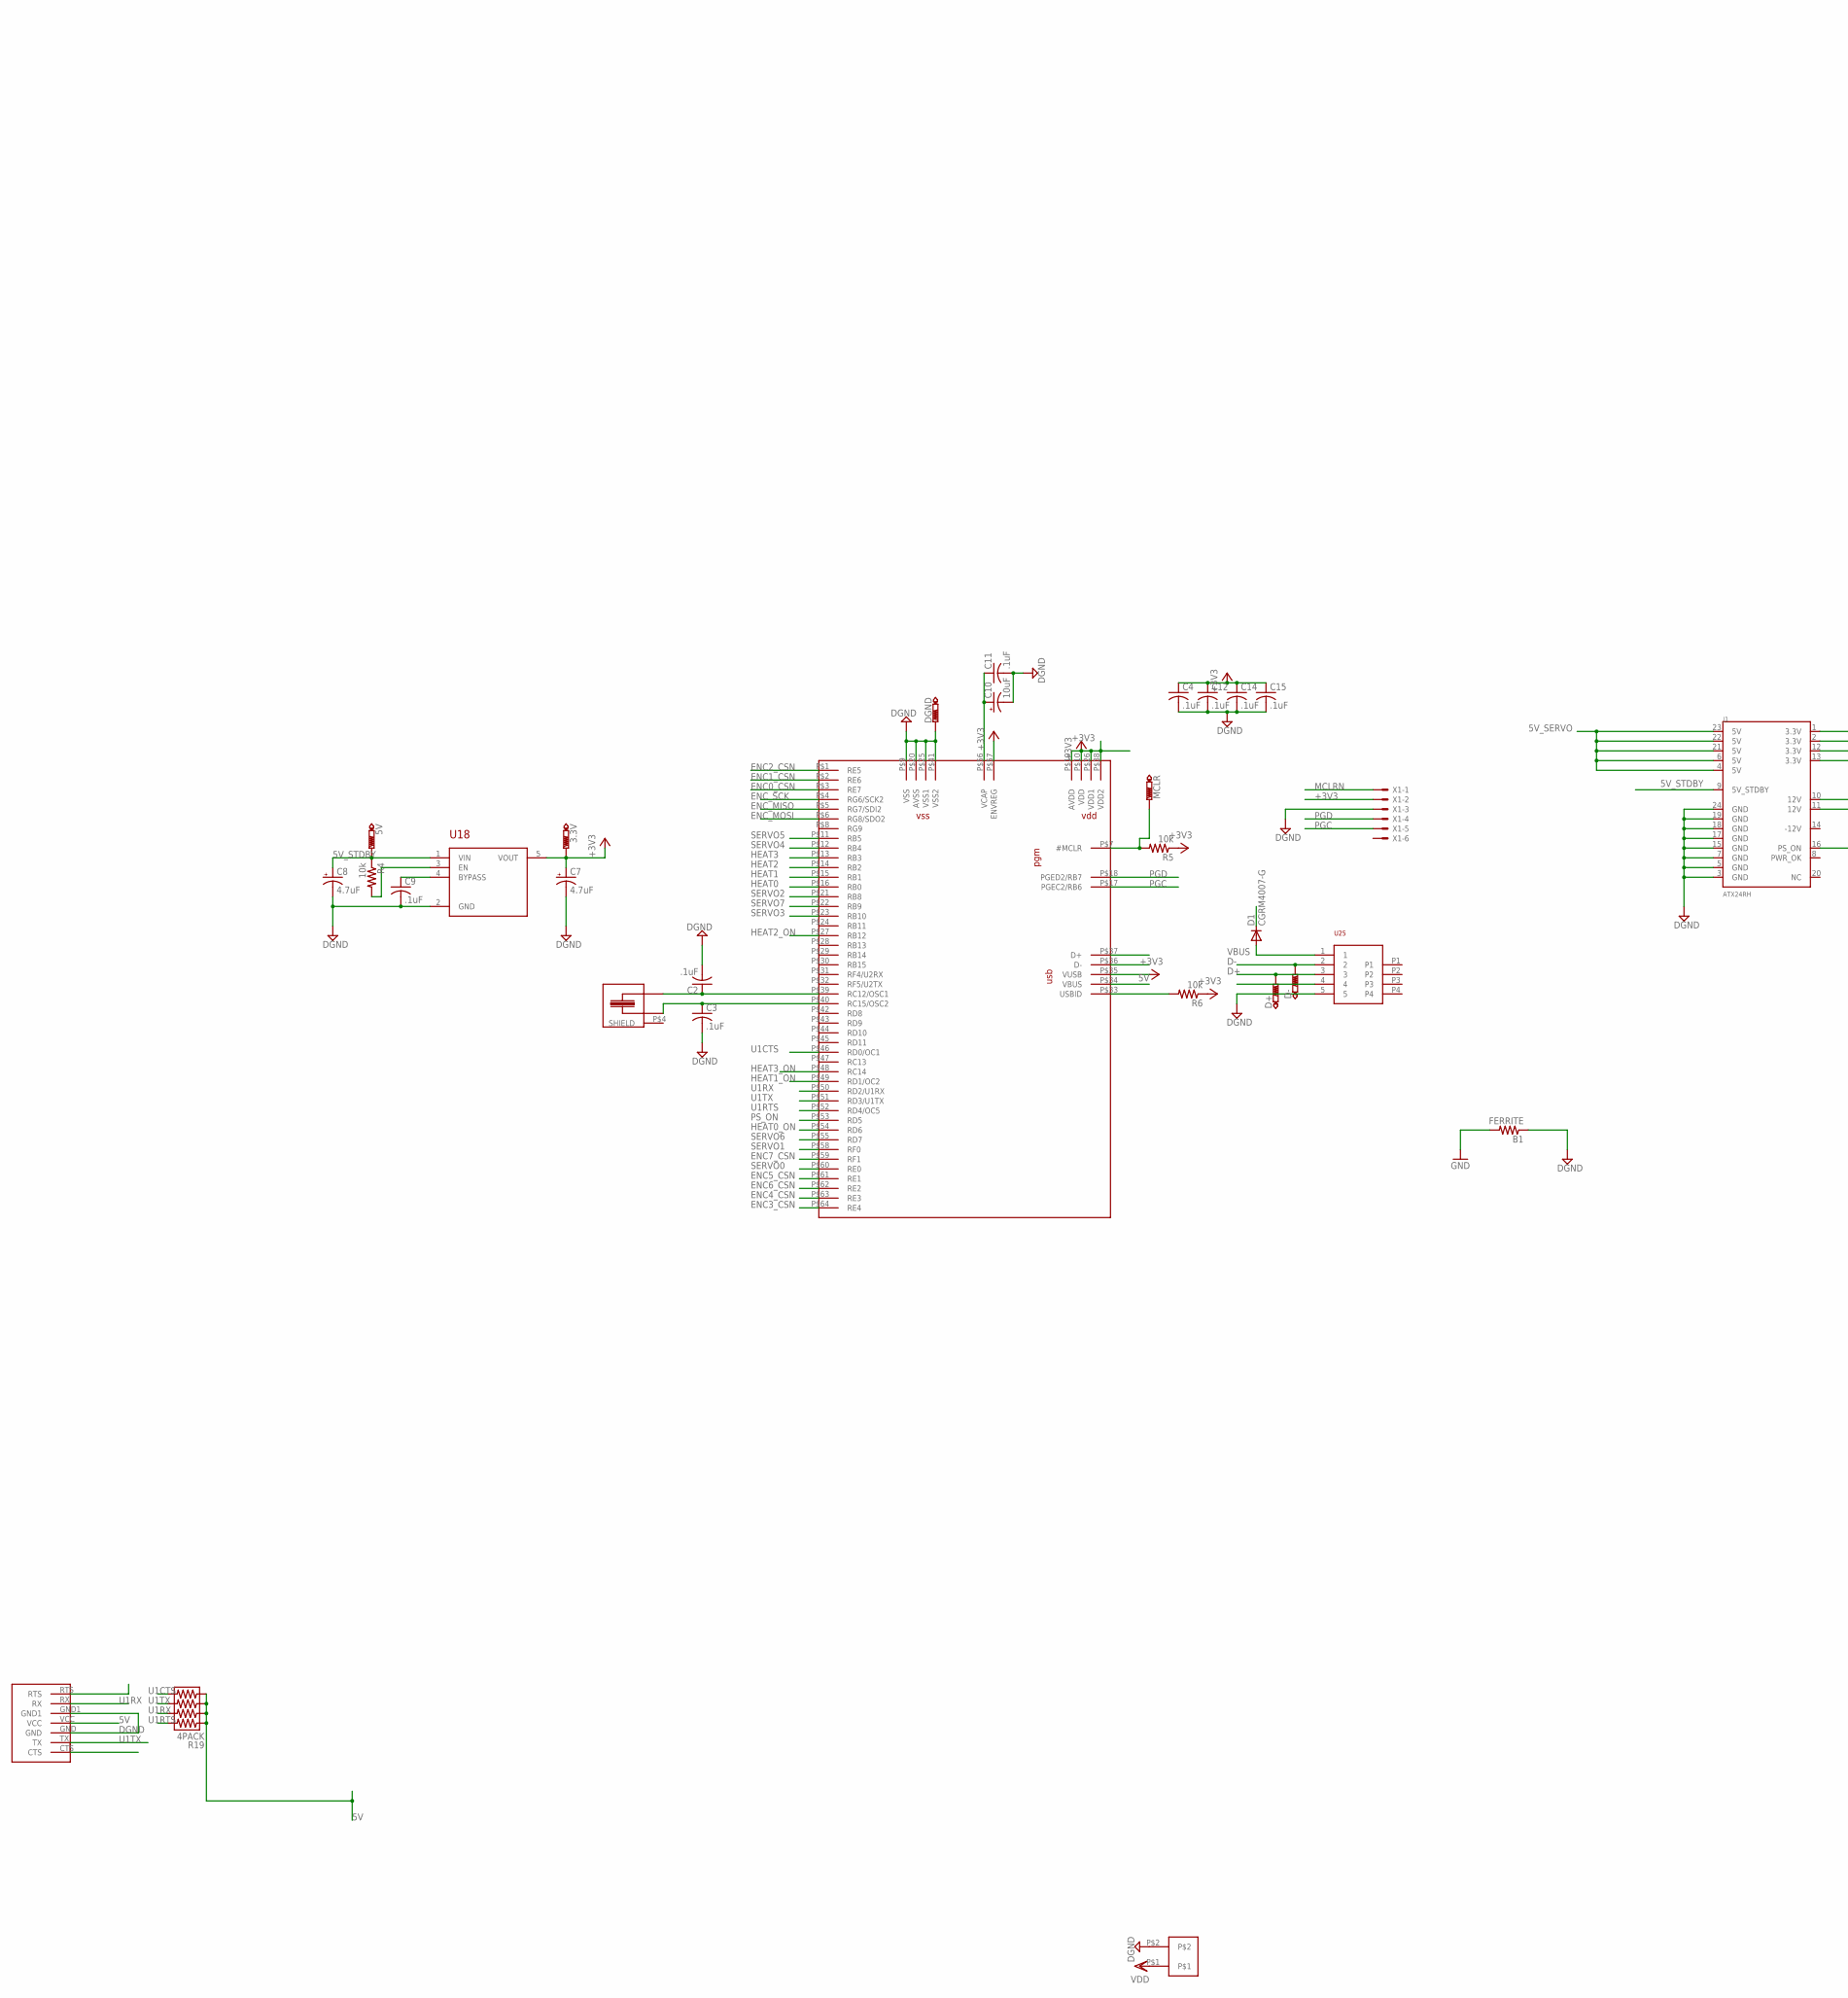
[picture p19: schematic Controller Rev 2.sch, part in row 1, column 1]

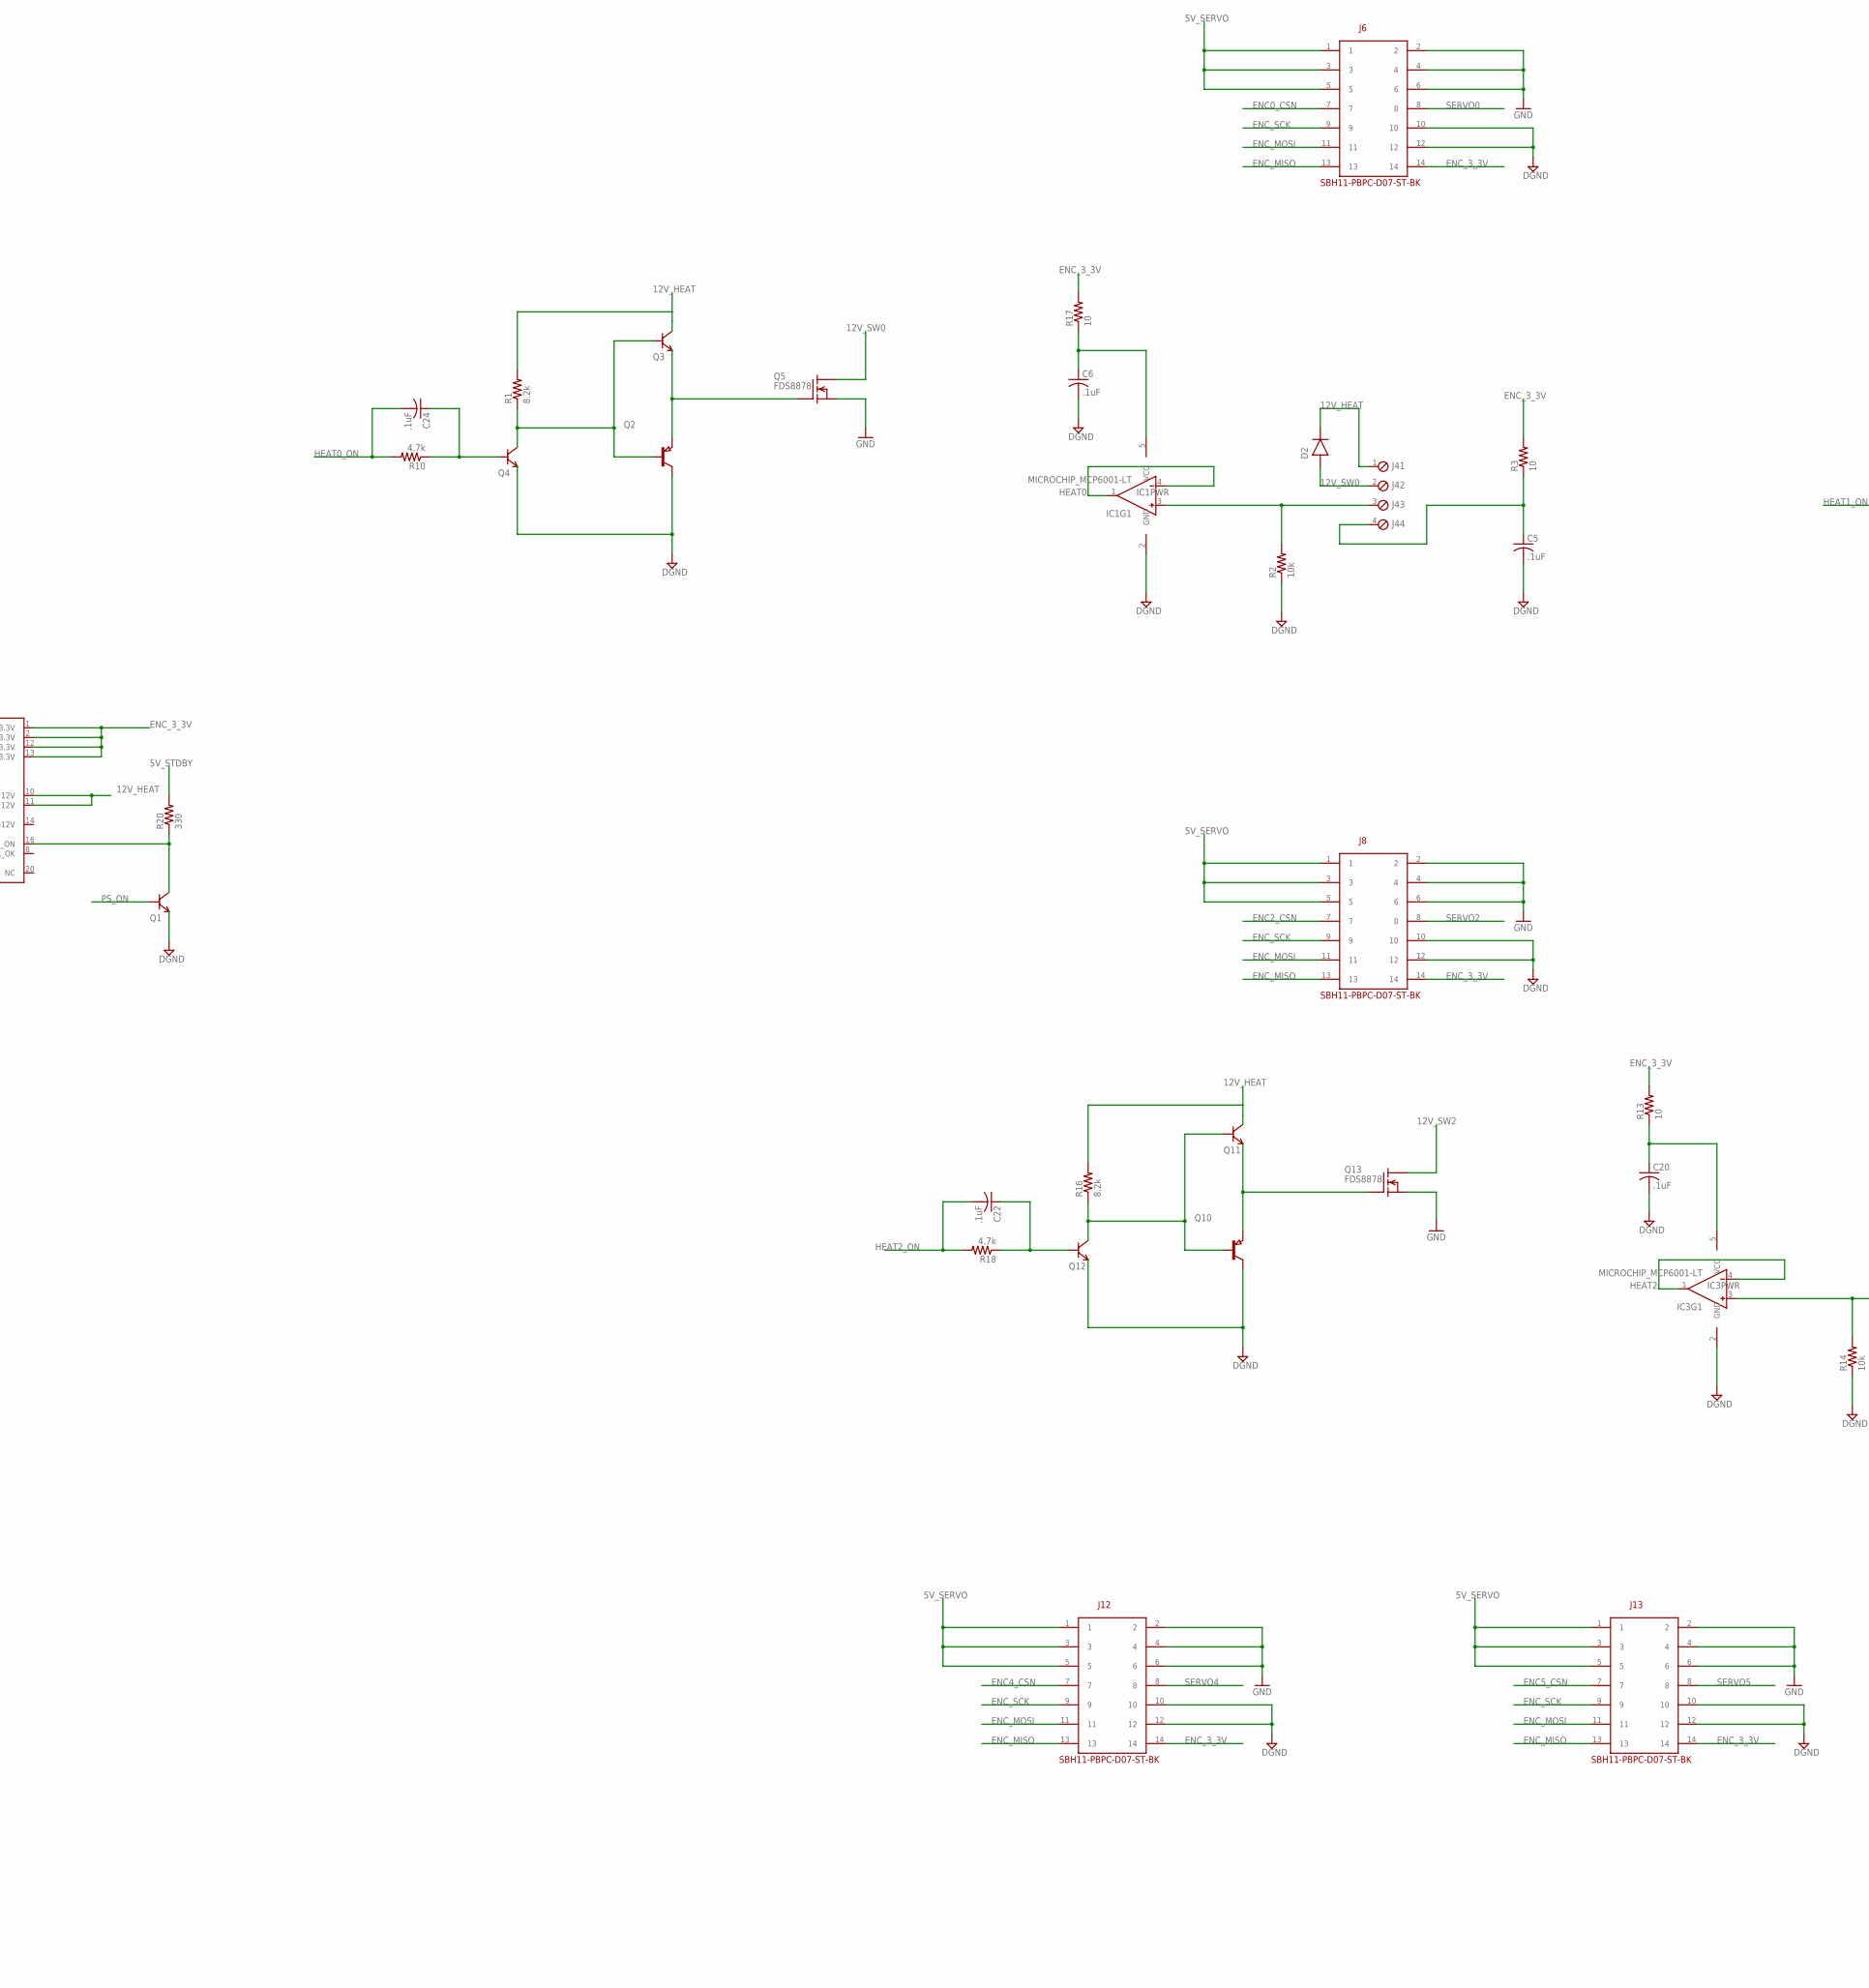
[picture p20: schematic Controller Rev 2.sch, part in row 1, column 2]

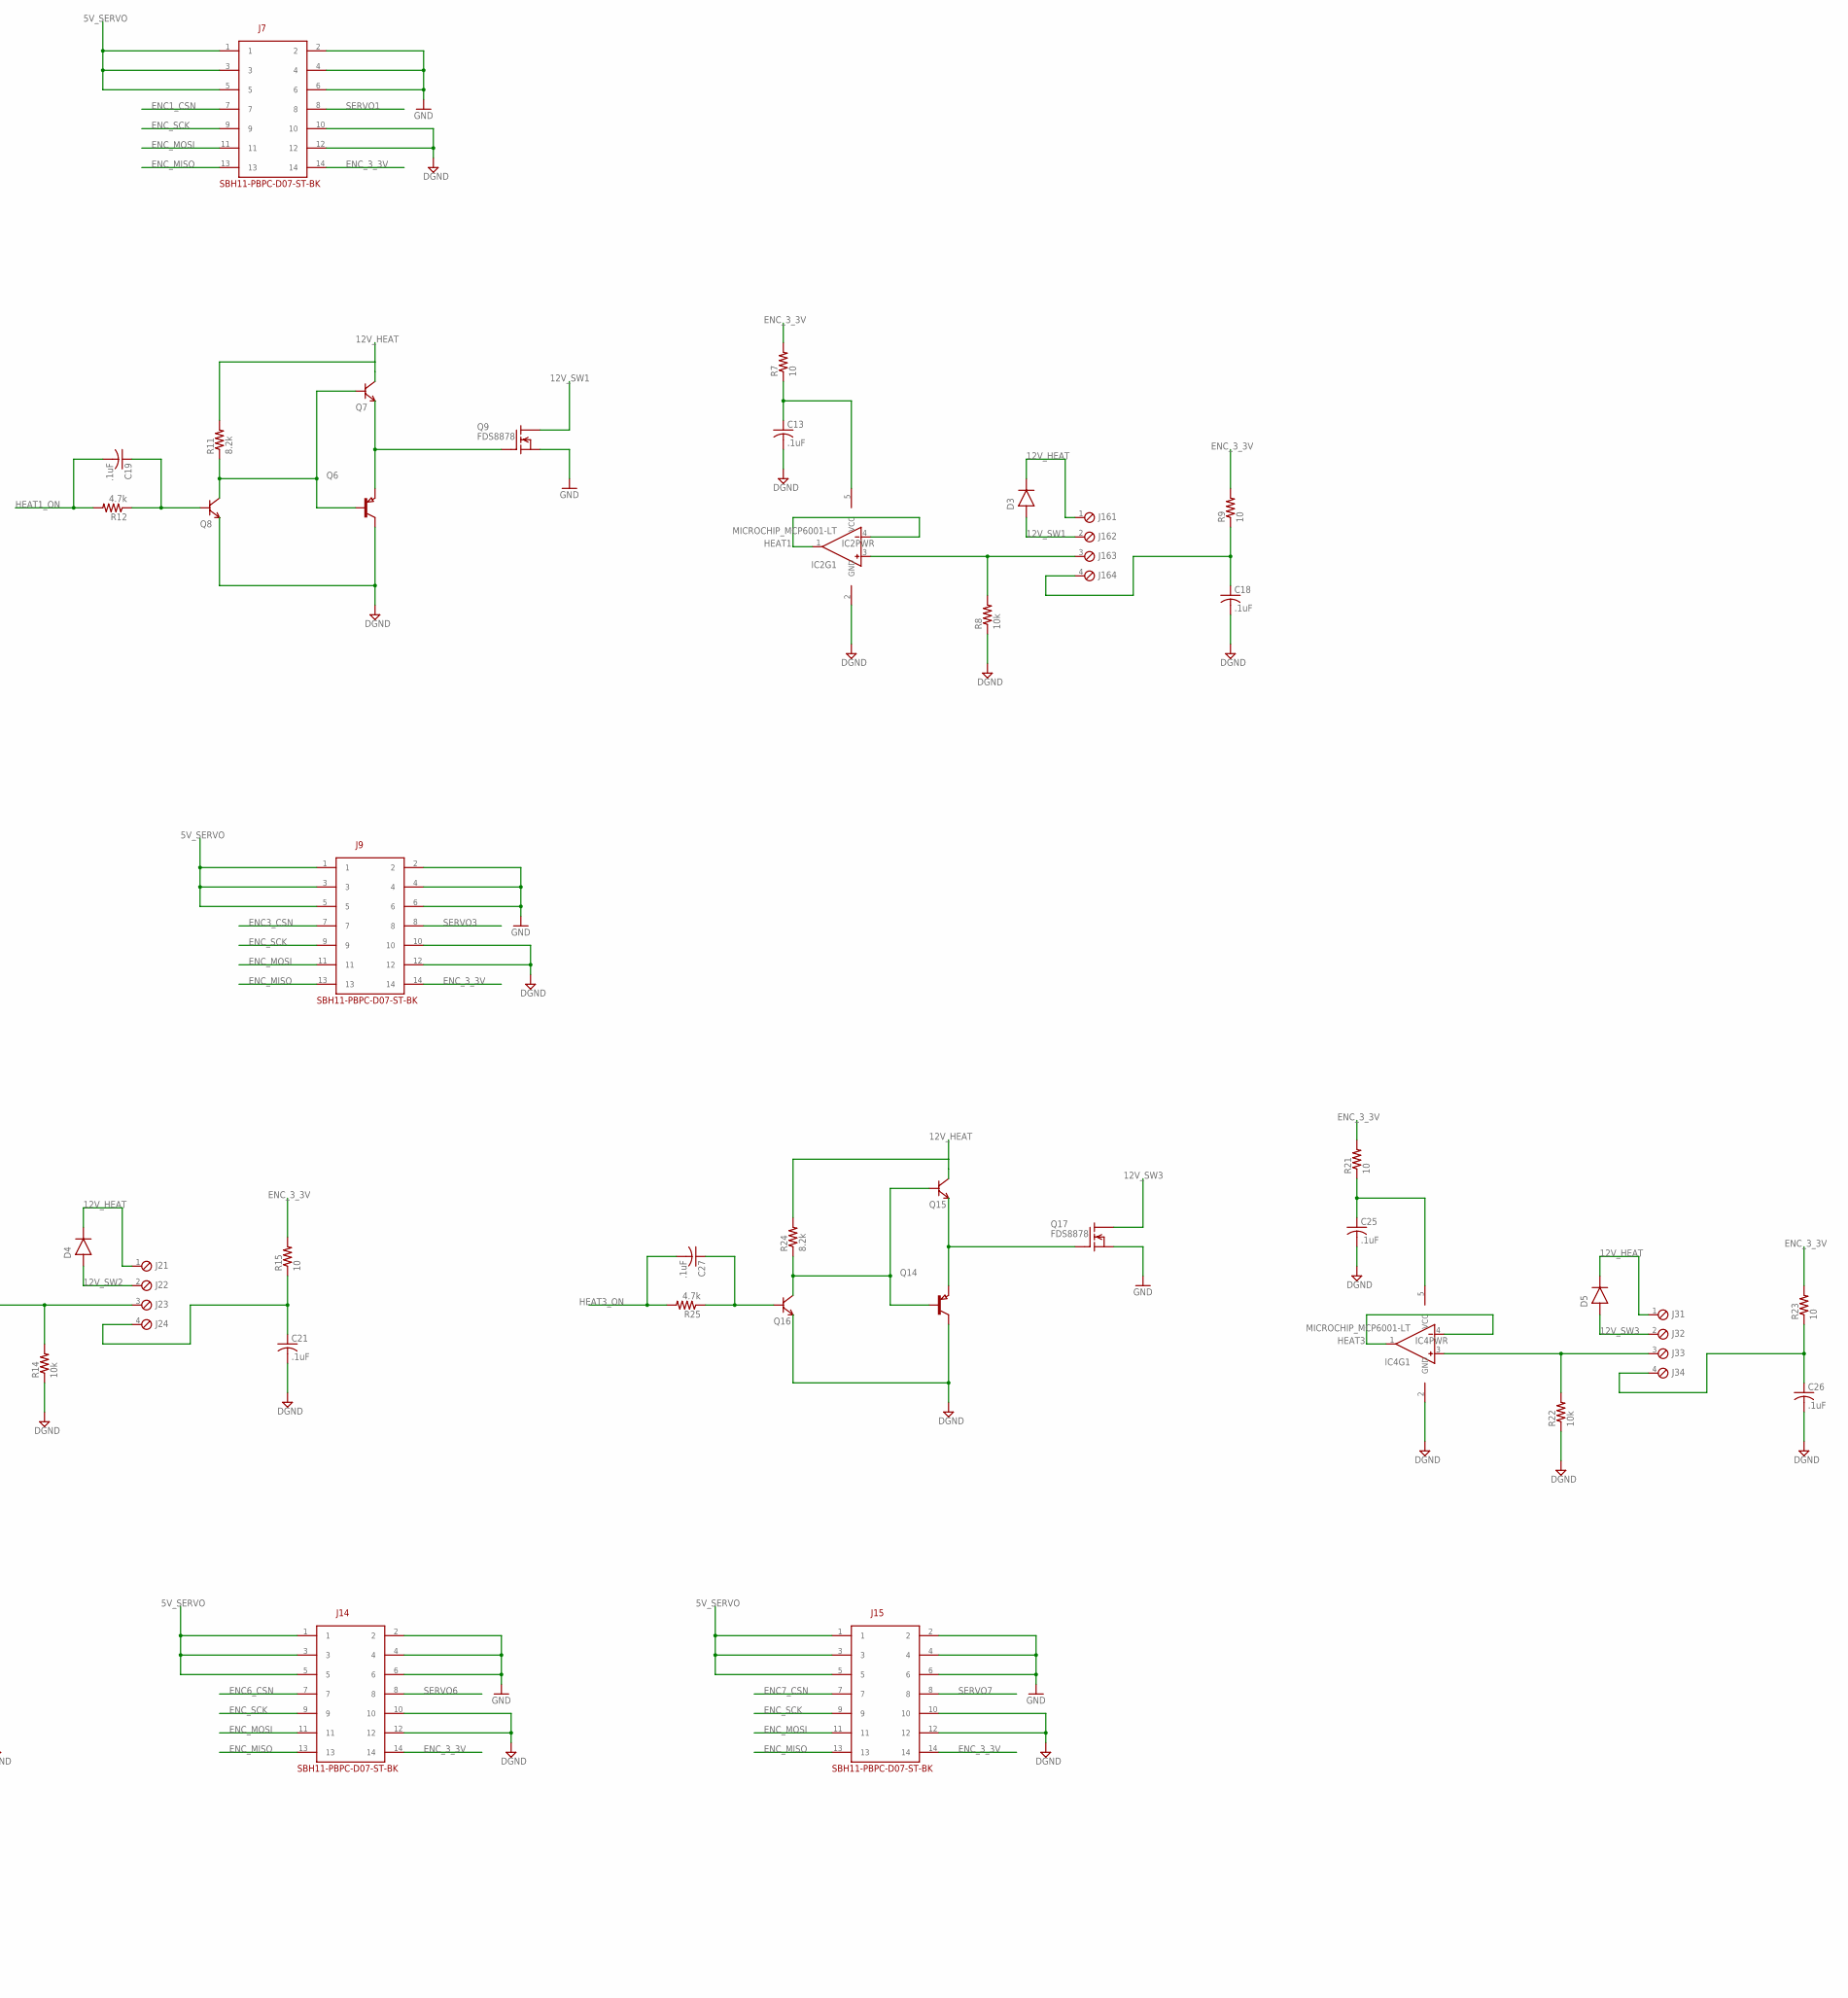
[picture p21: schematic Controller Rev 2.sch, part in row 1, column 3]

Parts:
3.3V, 5V: PTR1TP14R; TP14R
B1: FERRITE; R0603
C2, C3, C4, C5, C6, C11, C12, C13, C14, C15, C18, C19, C20, C21, C22, C24, C25, C26, C27: .1uF; C0603
C7, C8: 4.7uF; R/2012-12R
C9: .1uF; C0402
C10: 10uF; R/2012-12R
D1: CGRM4007-G; SOD-123_MINI-SMA
D2, D3, D4, D5: DISCRETE_DIODESMA; DISCRETE_SMA
D+: PTR1TP14R; TP14R
D-: PTR1TP14R; TP14R
DGND: PTR1B1,27; B1,27
IC1, IC2, IC3, IC4: MICROCHIP_MCP6001-LT; MICROCHIP_SC70-5-LT
J1: ATX24RH; ATX24_RIGHT_ANGLE
J2, J3, J4, J16: OSTVN04A150; 4POL254
J6, J7, J8, J9, J12, J13, J14, J15: SBH11-PBPC-D07-ST-BK
J10: WASP7PIN
MCLR: PTR1TP14R; TP14R
Q1, Q3, Q4, Q7, Q8, Q11, Q12, Q15, Q16: DISCRETE_MMBT3904LT1G; DISCRETE_SOT23
Q2, Q6, Q10, Q14: PNP-TRANSISTOR_SOT23; SOT23
Q5, Q9, Q13, Q17: FDS8878; SO-8
R1, R11, R16, R24: 8.2k; R0603
R2, R5, R6, R8, R14, R22: 10k; R0603
R3, R7, R9, R13, R15, R17, R21, R23: 10; R0603
R4: 10k; R0402
R10, R12, R18, R25: 4.7k; R0603
R19: 4PACK; 4PACK_0603
R20: 330; R0603
U3: PIC32-64TQFP64-2; TQFP64-2
U18: LDS3985XX33; SOT23-5
U25: 1734035-1_USB; 1734035-1_1734035
U$19: 2P; 2PTH
X1: 22-23-2061
X2: CMR3XXT; CMR309T

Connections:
5V: D1.C, J10.VCC, R19.R1B, R19.R2B, R19.R3B, R19.R4B, U3.P$34 (VBUS)
5V_SERVO: J1.4 (5V), J1.6 (5V), J1.21 (5V), J1.22 (5V), J1.23 (5V), J6.1, J6.3, J6.5, J7.1, J7.3, J7.5, J8.1, J8.3, J8.5, J9.1, J9.3, J9.5, J12.1, J12.3, J12.5, J13.1, J13.3, J13.5, J14.1, J14.3, J14.5, J15.1, J15.3, J15.5
5V_STDBY: 5V.TP, C8.+, J1.9 (5V_STDBY), R4.1, R20.2, U18.1 (VIN)
12V_HEAT: D2.C, D3.C, D4.C, D5.C, J1.10 (12V), J1.11 (12V), J2.1, J3.1, J4.1, J16.1, Q3.3 (C), Q7.3 (C), Q11.3 (C), Q15.3 (C), R1.2, R11.2, R16.2, R24.2
12V_SW0: D2.A, J4.2, Q5.5 (D), Q5.6 (D), Q5.7 (D), Q5.8 (D)
12V_SW1: D3.A, J16.2, Q9.5 (D), Q9.6 (D), Q9.7 (D), Q9.8 (D)
12V_SW2: D4.A, J2.2, Q13.5 (D), Q13.6 (D), Q13.7 (D), Q13.8 (D)
12V_SW3: D5.A, J3.2, Q17.5 (D), Q17.6 (D), Q17.7 (D), Q17.8 (D)
+3V3: 3.3V.TP, C4.1, C7.+, C12.1, C14.1, C15.1, R5.1, R6.1, U3.P$10 (VDD), U3.P$19 (AVDD), U3.P$26 (VDD1), U3.P$35 (VUSB), U3.P$38 (VDD2), U3.P$57 (ENVREG), U18.5 (VOUT), X1.2
D+: D+.TP, U3.P$37 (D+), U25.3
D-: D-.TP, U3.P$36 (D-), U25.2
DGND: B1.1, C2.2, C3.2, C4.2, C5.2, C6.2, C7.-, C8.-, C9.2, C10.-, C11.2, C12.2, C13.2, C14.2, C15.2, C18.2, C20.2, C21.2, C25.2, C26.2, DGND.PP, IC1.2 (GND), IC2.2 (GND), IC3.2 (GND), IC4.2 (GND), J1.3 (GND), J1.5 (GND), J1.7 (GND), J1.15 (GND), J1.17 (GND), J1.18 (GND), J1.19 (GND), J1.24 (GND), J6.10, J6.12, J7.10, J7.12, J8.10, J8.12, J9.10, J9.12, J10.GND, J10.GND1, J12.10, J12.12, J13.10, J13.12, J14.10, J14.12, J15.10, J15.12, Q1.2 (E), Q2.3 (C), Q4.2 (E), Q6.3 (C), Q8.2 (E), Q10.3 (C), Q12.2 (E), Q14.3 (C), Q16.2 (E), R2.1, R8.1, R14.1, R22.1, U3.P$9 (VSS), U3.P$20 (AVSS), U3.P$25 (VSS1), U3.P$41 (VSS2), U18.2 (GND), U25.5, U$19.P$2, X1.3
ENC0_CSN: J6.7, U3.P$3 (RE7)
ENC1_CSN: J7.7, U3.P$2 (RE6)
ENC2_CSN: J8.7, U3.P$1 (RE5)
ENC3_CSN: J9.7, U3.P$64 (RE4)
ENC4_CSN: J12.7, U3.P$63 (RE3)
ENC5_CSN: J13.7, U3.P$61 (RE1)
ENC6_CSN: J14.7, U3.P$62 (RE2)
ENC7_CSN: J15.7, U3.P$59 (RF1)
ENC_3_3V: J1.1 (3.3V), J1.2 (3.3V), J1.12 (3.3V), J1.13 (3.3V), J6.14, J7.14, J8.14, J9.14, J12.14, J13.14, J14.14, J15.14, R3.2, R7.2, R9.2, R13.2, R15.2, R17.2, R21.2, R23.2
ENC_MISO: J6.13, J7.13, J8.13, J9.13, J12.13, J13.13, J14.13, J15.13, U3.P$5 (RG7/SDI2)
ENC_MOSI: J6.11, J7.11, J8.11, J9.11, J12.11, J13.11, J14.11, J15.11, U3.P$6 (RG8/SDO2)
ENC_SCK: J6.9, J7.9, J8.9, J9.9, J12.9, J13.9, J14.9, J15.9, U3.P$4 (RG6/SCK2)
GND: B1.2, J6.2, J6.4, J6.6, J7.2, J7.4, J7.6, J8.2, J8.4, J8.6, J9.2, J9.4, J9.6, J12.2, J12.4, J12.6, J13.2, J13.4, J13.6, J14.2, J14.4, J14.6, J15.2, J15.4, J15.6, Q5.1 (S), Q5.2 (S), Q5.3 (S), Q9.1 (S), Q9.2 (S), Q9.3 (S), Q13.1 (S), Q13.2 (S), Q13.3 (S), Q17.1 (S), Q17.2 (S), Q17.3 (S)
HEAT0: IC1.1 (OUT), IC1.4 (IN-), U3.P$16 (RB0)
HEAT0_ON: C24.2, R10.2, U3.P$54 (RD6)
HEAT1: IC2.1 (OUT), IC2.4 (IN-), U3.P$15 (RB1)
HEAT1_ON: C19.2, R12.2, U3.P$49 (RD1/OC2)
HEAT2: IC3.1 (OUT), IC3.4 (IN-), U3.P$14 (RB2)
HEAT2_ON: C22.2, R18.2, U3.P$27 (RB12)
HEAT3: IC4.1 (OUT), IC4.4 (IN-), U3.P$13 (RB3)
HEAT3_ON: C27.2, R25.2, U3.P$48 (RC14)
MCLRN: MCLR.TP, R5.2, U3.P$7 (#MCLR), X1.1
unnamed: C5.1, J4.4, R3.1
unnamed: R4.2, U18.3 (EN)
unnamed: C9.1, U18.4 (BYPASS)
unnamed: C3.1, U3.P$40 (RC15/OSC2), X2.P$3
unnamed: C10.+, C11.1, U3.P$56 (VCAP)
unnamed: C2.1, U3.P$39 (RC12/OSC1), X2.P$1
unnamed: IC2.3 (IN+), J16.3, R8.2
unnamed: C13.1, IC2.5 (VCC), R7.1
unnamed: C18.1, J16.4, R9.1
unnamed: IC1.3 (IN+), J4.3, R2.2
unnamed: Q6.1 (B), Q7.1 (B), Q8.3 (C), R11.1
unnamed: C19.1, Q8.1 (B), R12.1
unnamed: Q2.1 (B), Q3.1 (B), Q4.3 (C), R1.1
unnamed: C24.1, Q4.1 (B), R10.1
unnamed: Q6.2 (E), Q7.2 (E), Q9.4 (G)
unnamed: Q2.2 (E), Q3.2 (E), Q5.4 (G)
unnamed: IC3.3 (IN+), J2.3, R14.2
unnamed: C20.1, IC3.5 (VCC), R13.1
unnamed: C21.1, J2.4, R15.1
unnamed: Q10.1 (B), Q11.1 (B), Q12.3 (C), R16.1
unnamed: C6.1, IC1.5 (VCC), R17.1
unnamed: C22.1, Q12.1 (B), R18.1
unnamed: Q10.2 (E), Q11.2 (E), Q13.4 (G)
unnamed: IC4.3 (IN+), J3.3, R22.2
unnamed: C25.1, IC4.5 (VCC), R21.1
unnamed: C26.1, J3.4, R23.1
unnamed: Q14.1 (B), Q15.1 (B), Q16.3 (C), R24.1
unnamed: C27.1, Q16.1 (B), R25.1
unnamed: Q14.2 (E), Q15.2 (E), Q17.4 (G)
unnamed: J1.16 (PS_ON), Q1.3 (C), R20.1
PGC: U3.P$17 (PGEC2/RB6), X1.5
PGD: U3.P$18 (PGED2/RB7), X1.4
PS_ON: Q1.1 (B), U3.P$53 (RD5)
SERVO0: J6.8, U3.P$60 (RE0)
SERVO1: J7.8, U3.P$58 (RF0)
SERVO2: J8.8, U3.P$21 (RB8)
SERVO3: J9.8, U3.P$23 (RB10)
SERVO4: J12.8, U3.P$12 (RB4)
SERVO5: J13.8, U3.P$11 (RB5)
SERVO6: J14.8, U3.P$55 (RD7)
SERVO7: J15.8, U3.P$22 (RB9)
U1CTS: J10.CTS, R19.R4A, U3.P$46 (RD0/OC1)
U1RTS: J10.RTS, R19.R1A, U3.P$52 (RD4/OC5)
U1RX: J10.RX, R19.R2A, U3.P$50 (RD2/U1RX)
U1TX: J10.TX, R19.R3A, U3.P$51 (RD3/U1TX)
USBID: R6.2, U3.P$33 (USBID), U25.4
VBUS: D1.A, U25.1
VDD: U$19.P$1

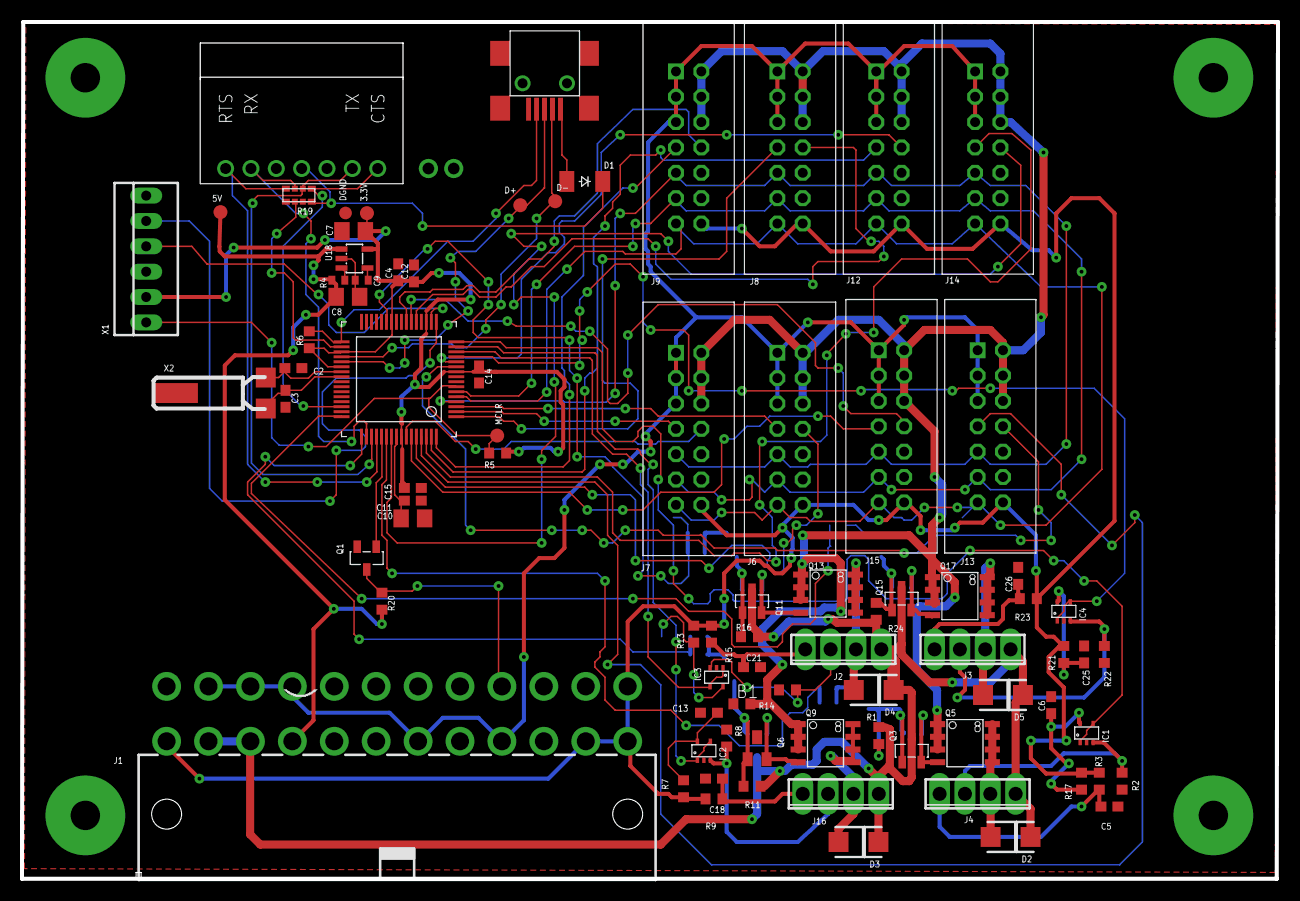
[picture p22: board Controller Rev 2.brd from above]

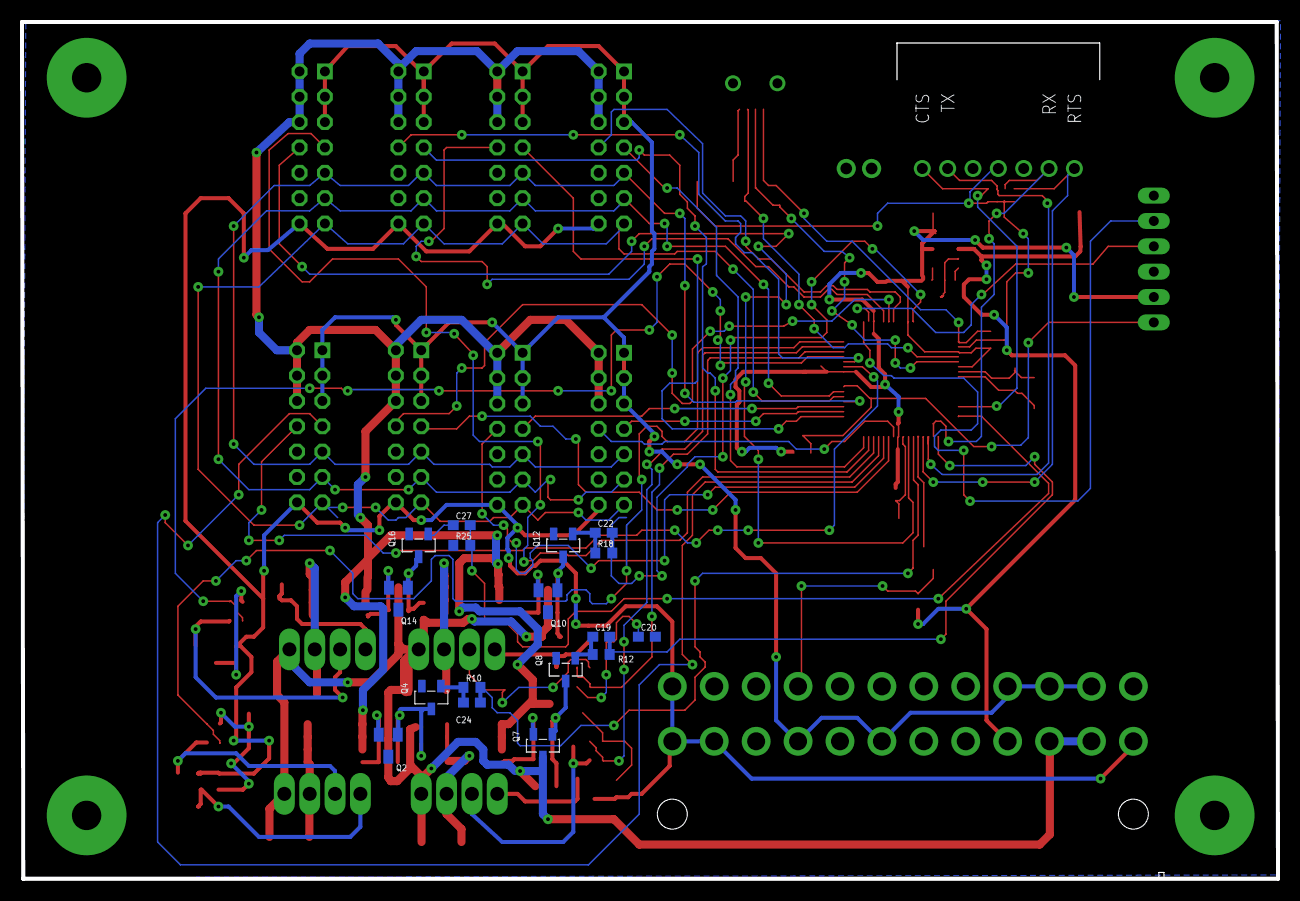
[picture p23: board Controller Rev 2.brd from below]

Board: 2 copper layers, 125.9 x 85.9 mm, 101 parts (17 on the bottom side), 81 nets.

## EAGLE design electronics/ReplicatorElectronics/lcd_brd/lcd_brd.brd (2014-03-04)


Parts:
J1: SBH11-PBPC-D17-ST-BK
J2: 101-00708-64
R5, R6, R7: 50k; R0603
R8, R9, R10, R11: 22; R0603
U$1: ST2040Y3WY-RSLW-F; ST0240Y3WY-RSLW-F

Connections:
A0: J1.23, U$1.33 (RS)
DB0: J1.10, U$1.30 (DB1)
DB1: J1.9, U$1.29 (DB2)
DB2: J1.12, U$1.28 (DB3)
DB3: J1.11, U$1.27 (DB4)
DB4: J1.14, U$1.26 (DB5)
DB5: J1.13, U$1.25 (DB6)
DB6: J1.16, U$1.24 (DB7)
DB7: J1.15, U$1.23 (DB8)
DB10: J1.7, U$1.22 (DB10)
DB11: J1.8, U$1.21 (DB11)
DB12: J1.5, U$1.20 (DB12)
DB13: J1.6, U$1.19 (DB13)
DB14: J1.1, U$1.18 (DB14)
DB15: J1.2, U$1.17 (DB15)
DB16: J1.4, U$1.16 (DB16)
DB17: J1.3, U$1.15 (DB17)
DGND: J1.30, J1.32, J1.34, J2.3, J2.6, J2.CGND1, J2.CGND2, J2.CGND3, J2.CGND4, R8.1, R9.1, R10.1, R11.1, U$1.1 (GND1), U$1.6 (GND6), U$1.7 (IM0), U$1.8 (IM3), U$1.35 (GND35), U$1.44 (GND44)
LCD_CS: J1.19, U$1.34 (CS)
LCD_RD: J1.17, U$1.31 (RD)
LCD_RST: J1.20, U$1.12 (RST)
LCD_WR: J1.18, U$1.32 (/WR)
unnamed: R8.2, U$1.39 (LEDK4)
unnamed: R9.2, U$1.40 (LEDK3)
unnamed: R10.2, U$1.41 (LEDK2)
unnamed: R11.2, U$1.42 (LEDK1)
SD_CSN: J1.24, J2.1, R7.1
SD_SP_MISO: J1.29, J2.7, R5.1
SD_SP_MOSI: J1.28, J2.2, R6.1
SD_SP_SCK: J1.27, J2.5
VCC: J1.31, J1.33, J2.4, R5.2, R6.2, R7.2, U$1.36 (IOVCC), U$1.37 (VCC37), U$1.38 (VCC38), U$1.43 (LEDA)
X+: J1.26, U$1.3 (X+)
X-: J1.21, U$1.5 (X-)
Y+: J1.25, U$1.4 (Y+)
Y-: J1.22, U$1.2 (Y-)


Board: 2 copper layers, 95.8 x 88.9 mm, 10 parts (0 on the bottom side), 35 nets.

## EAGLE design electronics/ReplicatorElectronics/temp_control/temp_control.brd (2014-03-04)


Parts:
C1, C5: 0.1uF; C0603
C2: 10uF; C0603
C3, C4: 1uF; C0603
D1: B340A-13-F; DISCRETE_SMA
J1: SBH11-PBPC-D05-ST-BK
J2: OSTVN04A150; 4POL254
LED1: RED; R0603
Q1: IRL640A; TO220
R1: 8.2k; R0603
R2: 4.7k; R0603
R3: 3.9k; R0603
R4, R5: 10k; R0603
R6, R7, R8: 0; R0603
R9: 10; R0603
T1, T2: MMBT2222A; SOT23-BEC
T3: MMBT3906LT1; SOT23-BEC
U1: AD8495; MSOP08

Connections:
CTRL: C1.2, J1.7, R2.2
GND: C3.2, C4.1, C5.2, J1.2, J1.4, J1.6, J1.8, LED1.1, Q1.3 (S), U1.2 (REF), U1.3 (-VS)
HEAT0: D1.A, J2.2, Q1.2 (D)
unnamed: LED1.2, R3.1
unnamed: C2.2, C3.1, R5.1, U1.1 (IN-)
unnamed: C1.1, R2.1, T2.B
unnamed: R1.1, T1.B, T2.C, T3.B
unnamed: C2.1, C4.2, R4.1, U1.8 (+IN)
unnamed: Q1.1 (G), R3.2, T1.E, T3.E
unnamed: C5.1, R9.1, U1.7 (+VS)
unnamed: T2.E, T3.C
unnamed: R6.1, U1.5 (SENSE), U1.6 (OUT)
OUT1: J2.3, R5.2, R8.1
OUT2: J2.4, R4.2, R7.1
THERM1: J1.9, R6.2, R8.2
THERM2: J1.10, R7.2
VCC: D1.C, J1.1, J1.3, J1.5, J2.1, R1.2, R9.2, T1.C


Board: 2 copper layers, 50.3 x 42.1 mm, 23 parts (0 on the bottom side), 17 nets.

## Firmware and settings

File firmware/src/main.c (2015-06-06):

/*********************************************************************
 *
 *                  Example application for the Microchip BSD stack HTTP Server
 *
 *********************************************************************
 * FileName:        main.c
 * Company:         Microchip Technology, Inc.
 *
 * Software License Agreement:
 *
 * The software supplied herewith by Microchip Technology Incorporated
 * (the ?Company?) for its dsPIC30F and PICmicro? Microcontroller is intended 
 * and supplied to you, the Company?s customer, for use solely and
 * exclusively on Microchip's dsPIC30F and PICmicro Microcontroller products. 
 * The software is owned by the Company and/or its supplier, and is
 * protected under applicable copyright laws. All rights are reserved.
 * Any use in violation of the foregoing restrictions may subject the
 * user to criminal sanctions under applicable laws, as well as to
 * civil liability for the breach of the terms and conditions of this
 * license.
 *
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
 *
 ********************************************************************/

#include "main.h"
#if !defined(Bootloader)
#ifdef USB_A0_SILICON_WORK_AROUND
	#pragma config UPLLEN   = OFF       // USB PLL Enabled (A0 bit inverted)
#else
	#pragma config UPLLEN   = ON        // USB PLL Enabled
#endif

#pragma config FPLLMUL  = MUL_20        // PLL Multiplier
#pragma config UPLLIDIV = DIV_2         // USB PLL Input Divider
#pragma config FPLLIDIV = DIV_2         // PLL Input Divider
#pragma config FPLLODIV = DIV_1         // PLL Output Divider
#pragma config FPBDIV   = DIV_1         // Peripheral Clock divisor

#pragma config FWDTEN   = OFF           // Watchdog Timer
//#pragma config FWDTEN   = ON          // Watchdog Timer

#pragma config WDTPS    = PS2048           // Watchdog Timer Postscale
#pragma config FCKSM    = CSDCMD        // Clock Switching & Fail Safe Clock Monitor
#pragma config OSCIOFNC = OFF           // CLKO Enable
#pragma config POSCMOD  = HS            // Primary Oscillator
#pragma config IESO     = ON            // Internal/External Switch-over
#pragma config FSOSCEN  = OFF            // Secondary Oscillator Enable (KLO was off)
#pragma config FNOSC    = PRIPLL        // Oscillator Selection
#pragma config CP       = OFF           // Code Protect
#pragma config BWP      = OFF           // Boot Flash Write Protect
#pragma config PWP      = OFF           // Program Flash Write Protect
#pragma config ICESEL   = ICS_PGx2      // ICE/ICD Comm Channel Select
#pragma config DEBUG    = OFF            // Background Debugger Enable

#if defined(__32MX795F512L__)
    #pragma config FVBUSONIO = OFF //Shuts off control of VBUSON pin on RB5
#endif

#endif

#define SYS_FREQ 			(80000000L)
//#define CALIBRATE_SERVO
//#define CALIBRATE
//#define NO_PID
//#define TEST_MOTION
//#define EXTRUDER_TEST

///////////////////////////////////////////////////////
const uint8_t MY_MAC_ADDRESS[]={0x74,0xf7,0x26,0x01,0x01,0x01};
extern const MAC_ADDR Broadcast __attribute__ ((section (".scs_global_var")));
extern MAC_ADDR MyMAC __attribute__ ((section (".scs_global_var")));


//  const unsigned char deltaNSName[] = "bcs.delta.*;0.3;;";
//  const unsigned char printNSName[]  = "bcs.printer.*;0.3;;";

  BowlerPacket MyPacket;
  RunEveryData pidRobotAsyncTimer ={0,10};

//  RunEveryData pos ={0,5};


  float height = 0;
  int j=0,i=0;


uint8_t Bowler_Server_Local(BowlerPacket * Packet){
  
        Print_Level l = getPrintLevel();
        //setPrintLevelNoPrint();
	if (GetBowlerPacket_arch(Packet)){
            setLED(0,1,1);
                if(Packet->use.head.RPC != _PNG){
                    //println_I("Got:");printPacket(Packet,INFO_PRINT);
                }
		if ( (CheckAddress(MyMAC.v,Packet->use.head.MAC.v) == true)  || ((CheckAddress((uint8_t *)Broadcast.v,(uint8_t *)Packet->use.head.MAC.v) == true)  )) {
                        float start=getMs();
                        Process_Self_Packet(Packet);
                        if(getMs()-start>5){
                            println_E("Process too long: ");p_fl_E(getMs()-start);
                        }
			for (i=0;i<6;i++){
				Packet->use.head.MAC.v[i]=MyMAC.v[i];
			}
			SetCRC(Packet);
                        start=getMs();
			PutBowlerPacket(Packet);
                        if(getMs()-start>5){
                            println_E("Return too long: ");p_fl_E(getMs()-start);
                        }
                         if(Packet->use.head.RPC != _PNG){
                            //println_I("Response:");printPacket(Packet,INFO_PRINT);
                         }
		}else{
			//println_I("Packet not addressed to me: ");printByteArray(Packet->use.head.MAC.v,6); print_I(" is not mine: ");printByteArray(MyMAC.v,6);
		}

                setPrintLevel(l);
                setLED(0,0,1);
		return true; 
	}//Have a packet
        //setLED(0,0,1);
        setPrintLevel(l);
	return false; 
}


void hardwareInit(){

     // Configure the device for maximum performance but do not change the PBDIV
	// Given the options, this function will change the flash wait states, RAM
	// wait state and enable prefetch cache but will not change the PBDIV.
	// The PBDIV value is already set via the pragma FPBDIV option above..
	SYSTEMConfig(SYS_FREQ, SYS_CFG_WAIT_STATES | SYS_CFG_PCACHE);
        SYSTEMConfigPerformance(80000000);
        
        resetButtionInit();

        ATX_DISENABLE();
        CloseTimer2();
        initLEDs();

        setLED(0,0,0);
        //while(1);
        Pic32_Bowler_HAL_Init();

	Bowler_Init();
        //clearPrint();
        println_I("\n\n\nStarting PIC initialization");
        enableFlashStorage(true);
        FlashGetMac(MyMAC.v);


        DelayMs(2000);//This si to prevent runaway during programming
	// enable driven to 3.3v on uart 1
	mPORTDOpenDrainClose(BIT_3); mPORTFOpenDrainClose(BIT_5);

	char macStr[13];

	for (i=0;i<6;i++){
		macStr[j++]=GetHighNib(MyMAC.v[i]);
		macStr[j++]=GetLowNib(MyMAC.v[i]);
	}
	macStr[12]=0;
	println_I("MAC address is =");
	print_I(macStr);
	char * dev = "CNCBoard";
        println_I(dev);
	//This Method calls INTEnableSystemMultiVectoredInt();
	usb_CDC_Serial_Init(dev,macStr,0x04D8,0x0001);

       
        addNamespaceToList((NAMESPACE_LIST *)getBcsCartesianNamespace());
        addNamespaceToList((NAMESPACE_LIST *)getNeuronroboticsPidRTD());
        addNamespaceToList((NAMESPACE_LIST *)getBcsPidNamespace());


        ATX_ENABLE(); // Turn on ATX Supply, Must be called before talking to the Encoders!!


        println_I("Starting Encoders");
        initializeEncoders();// Power supply must be turned on first

        println_I("Starting Heater");
        initializeHeater();

        println_I("Starting Servos");
        initServos();

#if !defined(NO_PID)
        println_I("Starting PID");
        initPIDLocal();
#endif
        DelayMs(100);
        initializeCartesianController();
#if defined(CALIBRATE_ON_BOOT)
        if(     GetPIDCalibrateionState(linkToHWIndex(0))!=CALIBRARTION_DONE&&
                GetPIDCalibrateionState(linkToHWIndex(1))!=CALIBRARTION_DONE&&
                GetPIDCalibrateionState(linkToHWIndex(2))!=CALIBRARTION_DONE

                    ){
            for(i=0;i<numPidMotors;i++){
                SetPIDEnabled(i,true) ;
            }

            println_I("Running calibration for kinematics axis");
            runPidHysterisisCalibration(linkToHWIndex(0));
            runPidHysterisisCalibration(linkToHWIndex(1));
            runPidHysterisisCalibration(linkToHWIndex(2));

            DelayMs(100);//wait for ISR to fire and update all value
            OnPidConfigure(0);
        }else{
            println_W("Axis are already calibrated");
        }
#else
        
        for (i = 0; i < numPidTotal; i++) {
            getPidGroupDataTable(i)->config.calibrationState = CALIBRARTION_DONE;
        }
        OnPidConfigure(0);
#endif
        
        pidRobotAsyncTimer.MsTime=getMs();
        //startHomingLinks();

        disableSerialComs(true) ;


}
boolean serVal =true; 

void bowlerSystem(){

    Bowler_Server_Local(&MyPacket);

    float diff = RunEvery(&pidRobotAsyncTimer);

    if(diff>0){
        RunNamespaceAsync(&MyPacket,&asyncCallback);
        if(diff>pidRobotAsyncTimer.setPoint){
            println_E("Time diff ran over! ");p_fl_E(diff);
            pidRobotAsyncTimer.MsTime=getMs();
        }
         cartesianAsync();
    }

}

boolean printCalibrations = false; 
boolean toggle = false;
boolean idleState=false;
int main(){
    setPrintLevelWarningPrint();
    hardwareInit();
    //setPrintLevelInfoPrint();
    //setPrintLevelWarningPrint();
    //setPrintLevelNoPrint();
    
    RunEveryData loop = {0.0,10.0};
    int i=0;
    for(;i<numPidMotors;i++)
        SetPIDEnabled(i,false);
    while(1){

        if (getResetButton()==1){
            setPrintLevelErrorPrint();
		p_int_E(0);print_E(" Reset Button Pressed from loop");
		//SetColor(1,1,1);
		U1CON = 0x0000;
		DelayMs(100);
		Reset();
	}
 #if defined(CALIBRATE_ON_BOOT)
        if(     GetPIDCalibrateionState(linkToHWIndex(0))==CALIBRARTION_DONE&&
                GetPIDCalibrateionState(linkToHWIndex(1))==CALIBRARTION_DONE&&
                GetPIDCalibrateionState(linkToHWIndex(2))==CALIBRARTION_DONE

                ){
            if(printCalibrations == false ){
                printCalibrations = true;
                int index=0;
                for(index=0;index<3;index++){
                    int group = linkToHWIndex(index);
                    println_E("For Axis ");p_int_E(group);
                    print_E(" upper: ");p_int_E(getPidGroupDataTable(group)->config.upperHistoresis);
                    print_E(" lower: ");p_int_E(getPidGroupDataTable(group)->config.lowerHistoresis);
                    print_E(" stop: ");p_int_E(getPidGroupDataTable(group)->config.stop);
                }
                startHomingLinks();
                //Print_Level l= getPrintLevel();

                //setPrintLevelInfoPrint();
                printCartesianData();
                int i;
                for(i=0;i<numPidMotors;i++){
                    printPIDvals(i);
                }
            }else{
                setLED(0,0,1);
            }
            //setPrintLevel(l);
        }else{
            if(RunEvery(&loop)>0){
                setLED(printCalibrations?0:1,toggle,printCalibrations);
                toggle = toggle?0:1;
            }
        }
#endif
        if(RunEvery(&loop)>0){
            float diff =(getMs()-getLastPacketTime());
            boolean idle = ((diff>1000)||(getMs()<1000))?TRUE:FALSE;
            if(idleState !=idle ){
                idleState=idle;
                if(idleState==TRUE){
                    println_W("Stopping motors");
                     setLED(1,0,1);
                    int i=0;
                    for(;i<numPidMotors;i++)
                        SetPIDEnabled(i,false);
                    resetUsbSystem();
                }else{
                    println_W("Coms safe for motors");
                    setLED(0,0,1);
                }
            }
        }
       
        bowlerSystem();
    }
}

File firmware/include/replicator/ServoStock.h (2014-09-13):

/* 
 * File:   ReplicatorHeader.h
 * Author: hephaestus
 *
 * Created on July 29, 2012, 4:39 PM
 */

#ifndef REPLICATORHEADER_H
#define	REPLICATORHEADER_H
#include "arch/pic32/Compiler.h"
#include "main.h"
#ifdef	__cplusplus
extern "C" {
#endif

typedef struct _DeltaConfig{
	float RodLength;
	float BaseRadius;
	float EndEffectorRadius;
	float MaxZ;
	float MinZ;
}DeltaConfig;

NAMESPACE_LIST * getBcsCartesianNamespace();
AbsPID * getFlashPidGroupDataTable();
boolean initFlashLocal();
void writeFlashLocal();



    // ATX MAcros and defines
#define     ATX_PWR_ON_TRIS    _TRISF0 // tris
#define     ATX_PWR_ON(s)      setPicIOPin(s, 'F',0)
#define     ATX_ENABLED        1

//#define     SPI_CLK_TRIS        _TRISG6 // tris
//#define     SPI_MISO_TRIS       _TRISG8 // tris
//#define     SPI_MOSI_TRIS       _TRISG7 // tris
#define     SPI_CLK_TRIS()        setPicIOTristateOutput('G',6) //_TRISG6 // tris
#define     SPI_MISO_TRIS()        setPicIOTristateInput('G',8)  //_TRISG8 // tris
#define     SPI_MOSI_TRIS()       setPicIOTristateOutput('G',7) //_TRISG7 // tris
#define     CloseSPIOpenCollector() mPORTGOpenDrainClose(BIT_6);\
                                        mPORTGOpenDrainClose(BIT_7);
#define     LED_RED_TRIS    setPicIOTristateOutput('D',10)
#define     LED_GRN_TRIS    setPicIOTristateOutput('D',11)
#define     LED_BLU_TRIS    setPicIOTristateOutput('D',0)


#define     initLEDs()      LED_RED_TRIS;LED_GRN_TRIS;LED_BLU_TRIS;
#define     setLED(r,g,b)  ioPortD(r>0?0:1, 10);ioPortD(g>0?0:1, 11);ioPortD(b>0?0:1, 0);


#define     resetButtionInit()      setPicIOTristateInput('F',5)//(_TRISF5)=INPUT; // for the reset sw
#define     getResetButton()        getPicIOPin('F',5)

#ifdef Rev4
    // eNCODER Connector macros and defines
    //PORT 0
#define     ENC0_CSN(s)          setPicIOPin(s, 'D',7)
#define     ENC0_CSN_TRIS      setPicIOTristateOutput('D',7)
#define     ENC0_SERVO_TRIS    setPicIOTristateOutput('B',15)
#define     ENC0_SERVO(s)        setPicIOPin(s, 'B',15)
    //PORT 1
#define     ENC1_CSN(s)          setPicIOPin(s, 'D',6)
#define     ENC1_CSN_TRIS      setPicIOTristateOutput('D',6)
#define     ENC1_SERVO_TRIS    setPicIOTristateOutput('B',14)
#define     ENC1_SERVO(s)        setPicIOPin(s, 'B',14)
    // Port 2
#define     ENC2_CSN(s)          setPicIOPin(s, 'D',5)
#define     ENC2_CSN_TRIS      setPicIOTristateOutput('D',5)
#define     ENC2_SERVO_TRIS    setPicIOTristateOutput('B',13)
#define     ENC2_SERVO(s)         setPicIOPin(s, 'B',13)
    // PORT 3
#define     ENC3_CSN(s)          setPicIOPin(s, 'D',4)
#define     ENC3_CSN_TRIS      setPicIOTristateOutput('D',4)
#define     ENC3_SERVO_TRIS    setPicIOTristateOutput('B',12)
#define     ENC3_SERVO(s)        setPicIOPin(s, 'B',12)
    // PORT 4
#define     ENC4_CSN(s)          setPicIOPin(s, 'E',5)
#define     ENC4_CSN_TRIS      setPicIOTristateOutput('E',5)
#define     ENC4_SERVO_TRIS    setPicIOTristateOutput('B',11)
#define     ENC4_SERVO(s)         setPicIOPin(s, 'B',11)
    // PORT 5
#define     ENC5_CSN(s)           setPicIOPin(s, 'E',6)
#define     ENC5_CSN_TRIS      setPicIOTristateOutput('E',6)
#define     ENC5_SERVO_TRIS    setPicIOTristateOutput('B',10)
#define     ENC5_SERVO(s)         setPicIOPin(s, 'B',10)
    //PORT 6
#define     ENC6_CSN(s)           setPicIOPin(s, 'E',7)
#define     ENC6_CSN_TRIS      setPicIOTristateOutput('E',7)
#define     ENC6_SERVO_TRIS    setPicIOTristateOutput('B',8)
#define     ENC6_SERVO(s)         setPicIOPin(s, 'B',8)
    //PORT 7
#define     ENC7_CSN(s)           setPicIOPin(s, 'G',9)
#define     ENC7_CSN_TRIS      setPicIOTristateOutput('G',9)
#define     ENC7_SERVO_TRIS    setPicIOTristateOutput('B',9)
#define     ENC7_SERVO(s)         setPicIOPin(s, 'B',9)


#define     setHeater0(s)         setPicIOPin(s, 'B',0)//
#define     HEATER_0_TRIS       setPicIOTristateOutput('B',0)

#define     setHeater1(s)        setPicIOPin(s, 'B',2)//
#define    HEATER_1_TRIS       setPicIOTristateOutput('B',2)

#define     setHeater2(s)        setPicIOPin(s, 'B',5)//
#define    HEATER_2_TRIS       setPicIOTristateOutput('B',5)

#define    HEATER_0_ADC         1
#define    HEATER_1_ADC         3
#define    HEATER_2_ADC         4

#elif defined( Rev3)
    // eNCODER Connector macros and defines
    //PORT 0
#define     ENC0_CSN(s)        setPicIOPin(s, 'E',7)//  setPicIOPin(s, 'E',7
#define     ENC0_CSN_TRIS      setPicIOTristateOutput('E',7)
#define     ENC0_SERVO_TRIS    setPicIOTristateOutput('B',12)
#define     ENC0_SERVO(s)      setPicIOPin(s, 'B',12)//  setPicIOPin(s, 'B',12
    //PORT 1
#define     ENC1_CSN(s)        setPicIOPin(s, 'D',7)//   setPicIOPin(s, 'D',7
#define     ENC1_CSN_TRIS      setPicIOTristateOutput('D',7)
#define     ENC1_SERVO_TRIS    setPicIOTristateOutput('B',10)
#define     ENC1_SERVO(s)      setPicIOPin(s, 'B',10)//setPicIOPin(s, 'B',10
    // Port 2
#define     ENC2_CSN(s)        setPicIOPin(s, 'G',9)//   setPicIOPin(s, 'G',9
#define     ENC2_CSN_TRIS      setPicIOTristateOutput('G',9)
#define     ENC2_SERVO_TRIS    setPicIOTristateOutput('B',15)
#define     ENC2_SERVO(s)      setPicIOPin(s, 'B',15)//setPicIOPin(s, 'B',15
    // PORT 3
#define     ENC3_CSN(s)        setPicIOPin(s, 'D',6)//    setPicIOPin(s, 'D',6
#define     ENC3_CSN_TRIS      setPicIOTristateOutput('D',6)
#define     ENC3_SERVO_TRIS    setPicIOTristateOutput('B',11)
#define     ENC3_SERVO(s)      setPicIOPin(s, 'B',11)//setPicIOPin(s, 'B',11
    // PORT 4
#define     ENC4_CSN(s)        setPicIOPin(s, 'E',5)//   setPicIOPin(s, 'E',5
#define     ENC4_CSN_TRIS      setPicIOTristateOutput('E',5)
#define     ENC4_SERVO_TRIS    setPicIOTristateOutput('B',14)
#define     ENC4_SERVO(s)      setPicIOPin(s, 'B',14)//setPicIOPin(s, 'B',14
    // PORT 5
#define     ENC5_CSN(s)        setPicIOPin(s, 'D',5)//    setPicIOPin(s, 'D',5
#define     ENC5_CSN_TRIS      setPicIOTristateOutput('D',5)
#define     ENC5_SERVO_TRIS    setPicIOTristateOutput('B',9)
#define     ENC5_SERVO(s)      setPicIOPin(s, 'B',9)//setPicIOPin(s, 'B',9
    //PORT 6
#define     ENC6_CSN(s)        setPicIOPin(s, 'E',6)//   setPicIOPin(s, 'E',6
#define     ENC6_CSN_TRIS      setPicIOTristateOutput('E',6)
#define     ENC6_SERVO_TRIS    setPicIOTristateOutput('B',13)
#define     ENC6_SERVO(s)      setPicIOPin(s, 'B',13)//setPicIOPin(s, 'B',13
    //PORT 7
#define     ENC7_CSN(s)        setPicIOPin(s, 'D',4)//   setPicIOPin(s, 'D',4
#define     ENC7_CSN_TRIS      setPicIOTristateOutput('D',4)
#define     ENC7_SERVO_TRIS    setPicIOTristateOutput('B',8)
#define     ENC7_SERVO(s)      setPicIOPin(s, 'B',8)//setPicIOPin(s, 'B',8

#define     setHeater0(s)      setPicIOPin(s, 'B',5)//
#define     HEATER_0_TRIS      setPicIOTristateOutput('B',5)

#define     setHeater1(s)      setPicIOPin(s, 'B',0)//
#define    HEATER_1_TRIS       setPicIOTristateOutput('B',0)

#define     setHeater2(s)      setPicIOPin(s, 'B',2)//
#define    HEATER_2_TRIS       setPicIOTristateOutput('B',2)
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

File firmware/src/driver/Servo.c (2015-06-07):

#include "main.h"

#define SERVO_BOUND 		0

#define NUM_SERVO 8

#define dataTableSize (NUM_SERVO)

//INTERPOLATE_DATA velocity[dataTableSize];
int position[dataTableSize];
int positionTemp[dataTableSize];
int sort[dataTableSize];
int lastValue=0;
int sortedIndex = 0;

//void delayLoop();

ServoState servoStateMachineCurrentState = LOW;

void runSort(){
    int i=0,k=0,x;
    int current;
    for(k=0;k<dataTableSize;k++){
        sort[k]=dataTableSize;
    }
    for(x=0;x<dataTableSize;x++){
        positionTemp[x]=position[x];
    }
    for(x=0;x<dataTableSize;x++){
        current = 256;
        for(i=0;i<dataTableSize;i++){
            int used= false; 
            for(k=0;k<dataTableSize;k++){
                if(sort[k]==i){
                    used=true; 
                }
            }
            if(positionTemp[i]<current && !used){
                sort[x]=i;

                current = positionTemp[i];
            }
        }
    }

}

void printSortedData(){
//    int x;
//    print_I("Servo Data \r\n[ ");
//
//    for(x=0;x<dataTableSize;x++){
//        p_int_I(positionTemp[x]);print_I(" , ");
//    }
//    print_I(" ] ");
//
//    print_I("\r\n[ ");
//
//    for(x=0;x<dataTableSize;x++){
//        p_int_I(sort[x]);print_I(" , ");
//    }
//    print_I(" ] ");
//
//    print_I("\r\n[ ");
//
//    for(x=0;x<dataTableSize;x++){
//        p_int_I(positionTemp[sort[x]]);print_I(" , ");
//    }
//    print_I(" ] ");
}

void setServoTimer(int value){
    if(value<1)
        value = 1;
    if(value>0xfffe)
        value = 0xfffe;
    //PR2 = value;
    OpenTimer2(T2_ON | T2_SOURCE_INT | T2_PS_1_256, value);
    ConfigIntTimer2(T2_INT_ON | T2_INT_PRIOR_7);
}

void setTimerLowTime(){
    setServoTimer(300*(18-(encoderIntegralSize/2)));
    servoStateMachineCurrentState = LOW;
}

void setTimerPreTime(){
    setServoTimer(285);
    servoStateMachineCurrentState = PRETIME;
}

void setTimerServoTicks(int value){
    setServoTimer((int)((float)value*1.4));
    servoStateMachineCurrentState = TIME;
}

#define MIN_SERVO 1


boolean setUpNextServo(){

    int diff = positionTemp[sort[sortedIndex]] - lastValue;
    lastValue = positionTemp[sort[sortedIndex]];
    if(diff<0){
        setPrintLevelErrorPrint();
//        println_E("Servo.c: Something is wrong!! Current minus last value is less then 0");
        while(1);
    }

    if(diff>MIN_SERVO){
        setTimerServoTicks(diff);
        return true; 
    }
    //Fall through for pin shut off
    servoStateMachineCurrentState = TIME;
    return false; 
}

void stopCurrentServo(){
    pinOff(sort[sortedIndex]);
    sortedIndex++;
    if(sortedIndex == dataTableSize){
        servoStateMachineCurrentState = FINISH;
        //fall through to finish
    }
}

void servoTimerEvent()
{
        //mPORTDToggleBits(BIT_3);
	//StartCritical();
        stopServos();
        int j;
        switch(servoStateMachineCurrentState){
            case LOW:
                updateAllEncoders();
                if(getRunPidIsr()){
                    RunPIDControl();
                    //Print_Level l = getPrintLevel();
                    interpolateZXY();
                    //setPrintLevelNoPrint();
                    
                }
                //runLinearInterpolationServo(start,stop);
                runSort();
                for (j=0;j<NUM_SERVO;j++){
                    pinOn(j);
                }
                lastValue = 0;
                sortedIndex=0;
                //1ms delay for all servos
                setTimerPreTime();
                return;
            case PRETIME:
                if(setUpNextServo())
                    return;
            case TIME:
                stopCurrentServo();
                if(servoStateMachineCurrentState == TIME){
                    if(setUpNextServo() == false) {
                        //fast stop for channels with the same value
                        servoTimerEvent();
                    }
                }
                //If there are still more channels to be turned off after the recoursion, break
                if(servoStateMachineCurrentState != FINISH)
                    return;

            case FINISH:
                setTimerLowTime();
                return;
        }
        //EndCritical();
}

void __ISR(_TIMER_2_VECTOR, ipl7) Timer2Handler(void){
    servoTimerEvent();
}

void stopServos(){
    CloseTimer2();
}

/**
 * Start the servo hardware
 */
void initServos(){

    SERVO_HW_INIT();

    if(getPrintLevel() == NO_PRINT){
        CloseUART1();
    }
    int i;
    for(i=0;i<dataTableSize;i++){
        pinOff(i);
        setServo(i,128,0);
    }
//    runLinearInterpolationServo(start,stop);
//    runSort();
//    for(i=0;i<numPidMotor;i++){
//       println_I("Servo Positions: ");p_sl_I(getServoPosition(i));
//    }
//    for(i=0;i<numPidMotor;i++){
//       println_I("Sorted Servo Positions index: ");p_sl_I(sort[i]); print_I(" value: ");p_sl_I(position[sort[i]]);
//    }


    setTimerLowTime();
}

/**
 * Set a setpoint for a servo with an intrerpolated time
 */
void setServo(uint8_t PIN, uint8_t val,float time){
    if(time<30)
            time=0;
//    velocity[PIN].setTime=time;
//    velocity[PIN].set=(float)val;
//    velocity[PIN].start=(float)position[PIN];
//    velocity[PIN].startTime=getMs();
//    if (val==position[PIN]){
//            velocity[PIN].setTime=0;
//    }
    position[PIN]=val;
    Print_Level l = getPrintLevel();

    //println_I("\tSrv ");p_int_I(PIN); print_I(" v=");p_int_I(val);
    setPrintLevel(l);
}

/**
 * get the current position of the servo
 */
uint8_t getServoPosition(uint8_t PIN){
    return position[PIN];
}

//void runLinearInterpolationServo(uint8_t blockStart,uint8_t blockEnd){
//	uint8_t i;
//	for (i=blockStart;i<blockEnd;i++){
//		//float ip = interpolate(&velocity[i],getMs());
//                float ip = position[i];
//		if(ip>(255- SERVO_BOUND)){
//			ip=(255- SERVO_BOUND);
//		}
//		if(ip<SERVO_BOUND){
//			ip=SERVO_BOUND;
//		}
//		int tmp = (int)ip;
//
//                position[i]= (BYTE) tmp;
//
//	}
//
//}

void SetDIO(uint8_t PIN, boolean state){
    if(!getPidGroupDataTable(PIN)->config.Enabled)
        state=0;

    switch(PIN){
    case 0:
            ENC0_SERVO( state);
            break;
    case 1:
            ENC1_SERVO(state);
            break;
    case 2:
        //if(getPrintLevel() == NO_PRINT)
            ENC2_SERVO(state);
            break;
    case 3:
        //if(getPrintLevel() == NO_PRINT)
            ENC3_SERVO(state);
            break;
    case 4:
            ENC4_SERVO(state);
            break;
    case 5:
            ENC5_SERVO(state);
            break;
    case 6:
            ENC6_SERVO(state);
            break;
    case 7:
            ENC7_SERVO(state);
            break;
    default:
            break;
    }
}

uint8_t pinOn(uint8_t pin){
    SetDIO(pin,1);
    return 1;
}

void pinOff(uint8_t pin){
    SetDIO(pin,0);
}
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

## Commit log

2012-02-24 Added Chipkit reference design eagle proj. Scraped components from design files and added them to library.
    [chipKIT Max32.brd, chipKIT Max32.sch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]
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2012-02-24 2/23/11: Added Rev. 2 Encoder Board. Fixes disconnect between layout and schematic, Header yet to be placed and routed.
    [MagEnc2.sch]
2012-02-24 2/23/11: Added Rev. 3 of Encoder Board. This layout is complete, pending design changes which add pass-through servo control signals.
    [MagEnc2.brd, MagEnc2.sch]
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2012-02-25 2/24/12: Added Rev. 1 Replicator Controller, Schematic ONLY. Still needs the following:
    - PHY
    - Magjack
    - Prg. Header
    - 3.3V LDO on 5V Standby Line
    - External Oscillator
    [rep_ctrlr.sch]
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2012-03-04 3/4/12: Rev. 4 Controller. Completed PHY, replaced placeholder connectors for PRG header and spool with real ones, swapped out 3.3V LDO with in-stock component of different package type, replaced 2mm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
    Note: 25 MHz crystal is a non-stock item in that family, needs replacement in Rev. 5.
    [rep_ctrlr.sch]
2012-03-08 3/7/12: Rev 4 of the Encoder Board. Added feed-through for servo, may yet need layout modifications to alter placement of encoder IC or size of mounting holes.
    [MagEnc2.brd, MagEnc2.sch]
2012-03-08 3/7/12: Added new symbols to reference designs folder, added Rev. 1 schematic and layout for heater relay card.
    [temp_control.brd, temp_control.sch]
2012-03-17 3/17/12: Rev. 02 Temp Control Board. Replaced 2x7 rectangular header with 0.100" pitch screw terminal, added high-side totem pole driver for MOSFET, added clearance holes for mounting screws. Swapped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
    [temp_control.brd, temp_control.sch]
2012-03-17 3/17/12: Rev. 5 of the Encoder Board. Moved connectors to back side of board, centered encoder on board, changed clearance hole size to fit 8-32 screws.
    [MagEnc2.brd]
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2012-03-31 3/31/12: Rev. 6 of the Encoder board. Modified 2x7 pin header decal, moved location of 1x3 pin header, generated DXF files (one with just mounting holes, another with holes and high-profile component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
    ~ 0.5 hrs invested.
    [MagEnc2.brd, MagEnc2.dxf, MagEnc2.sch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]
2012-03-31 3/31/12: Rev. 3 of temp control board. Modified 2x5 header symbol, generated DXF files (one with holes only, another with holes and high-profile parts).
    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
    [temp_control.brd, temp_control.dxf, temp_control.sch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]
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2012-04-15 Updated WorkspaceNavigator and connected print button to calls to slice/print given STL.
    [3007.stl, bottle.stl, cube.stl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]
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2012-04-29 4/29/12: Updated MagEnc2.dxf to include all PCB layers.
    [MagEnc2.dxf]
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2012-05-05 5/5/12: Routed good portion of the PHY. Work in progress.
    [rep_ctrlr.brd, rep_ctrlr.sch]
2012-05-09 5/8/12: First complete PHY layout attempt. Other parts of board still require routing.
    ~ 2 hrs.
    [rep_ctrlr.brd, rep_ctrlr.sch]
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2012-05-14 corrected SBH11 connector widths.
2012-05-14 5/13/12: Added level translator, added LCD board connector. Corrected connector widths - this required ripup of most traces associated with them. Began new attempt at PIC routing which should be more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
    ~ 3 hrs.
    [rep_ctrlr.sch]
2012-05-15 5/14/12: Began power rail routing and display connector routing.
    ~ 2 hrs
    [rep_ctrlr.brd, rep_ctrlr.sch]
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2012-05-16 5/15/12: Completed power routing, completed servo connector routing save for PIC traces (which now lead nearby PIC but do not connect to pins). Heater connectors and PIC IO routing remain largely unt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
    [rep_ctrlr.brd, rep_ctrlr.sch]
2012-05-17 5/16/12: All but PHY-PIC signals, encoder SPI bus (PIC pins only), servo signals (3.3V side only), and temperature inputs routed.
    ~ 4 hrs.
    [rep_ctrlr.brd, rep_ctrlr.sch]
2012-05-18 Replaced Preview3D with better implementation STLPreview, extending Canvas3D instead of Applet. Implemented various camera movements (zooming in and out along current view line, panning, etc). Extrac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
    [writerTest.stl]
2012-05-19 5/19/12: Corrected J1 connector width, updated DXF to indicate this.
    [temp_control.dxf, temp_control.sch]
2012-05-19 5/19/12: Corrected J1 connector width, regenerated DXF to indicate this.
    [MagEnc2.brd, MagEnc2.dxf, MagEnc2.sch]
2012-05-19 5/19/12: 18 PIC connections left. Ground currently fractured.
    ~3 hrs spent between last commit and this one.
    [rep_ctrlr.brd, rep_ctrlr.sch]
2012-05-22 5/21/12: Fixed GND plane. Still 18 PIC connections remaining...
    ~ 1 hr.
    [rep_ctrlr.brd]
2012-05-25 5/25/12: Updated to Rev. 6, with all components (except through-hole connectors) on topside of board, and some other minor cleanup. No change to hole or encoder placement.
    ~0.5 hr.
    [MagEnc2.brd]
2012-05-25 5/25/12: Brought all components topside, some minor cleanup. No change to placement of holes or large components.
    ~ 0.5 hr.
    [temp_control.brd]
2012-05-27 Subclassed TransformGroup into STLTransformGroup to give easier access to a few useful functions. Changed STLLoader and STLPreview classes accordingly. Added in functionality to turn facet outline on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
    [writerTest.stl]
2012-05-27 5/27/12: 5 PIC pins remain to be routed (3 encoder signals and encoder SPI MISO/MOSI), as well as buffers/passives around heater connectors. Cleanup will be required.
    ~ 6 hrs.
    [rep_ctrlr.brd, rep_ctrlr.sch]
2012-05-27 5/27/12: 3 PIC Pins remain (3 encoder CSN signals), as well as thermistor buffer routing at heater connectors. Pinswaps will be required on the PIC. DRC check reveals multiple conflicts which will re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
    [rep_ctrlr.brd]
2012-05-27 Divided several classes into more relevant packages (gui.navigator, gui.preview). Added functionality in STLObject to accept a Transform3D object and output an STLObject with the transform applied. A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
    [tempTransform.stl, writerTest.stl]
2012-05-27 Made small fix to way STLTransform calculates current mins and maxes given the current transform.
    [writerTest.stl]
2012-05-28 5/28/12: Preliminary placement and routing complete, need to clean up DRC errors.
    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
    [rep_ctrlr.brd, rep_ctrlr.sch]
2012-05-31 5/30/12: Preliminary layout finished! Ready for review by Alex.
    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
    [rep_ctrlr.brd, rep_ctrlr.sch]
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2012-06-04 6/3/12: Corrections to size reduction.
    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
    [MagEnc2.brd, MagEnc2.dxf]
2012-06-04 Fixed the issue where rotating camera with the mouse caused model to flip (problem with calculating new x and z values when moving camera up and down in STLPreview). Started reworking the Navigator t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
    [writerTest.stl]
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2012-06-07 Reworked WorkspaceNavigator system to better use JTree's DefaultTreeModel for updating the tree.
    [tempTransform.stl, writerTest.stl]
2012-06-08 5/8/12: Resolved refdes discrepancies, replaced unavailable components.
    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
    [rep_ctrlr.brd, rep_ctrlr.sch]
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2012-06-11 Updated to use nio.files package for simple file copying of STL's into the GUI.
    [writerTest.stl]
2012-06-11 Added in loading screen for previews. Extracted loading of previews to a thread so all GUI operations are not tied up when loading what may often be large stl files (such as 700.stl).
    [writerTest.stl]
2012-06-13 6/12/12: Added linearization circuit for potential thermocouple use. Can be DNP if not used.
    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
    [temp_control.brd, temp_control.dxf, temp_control.sch]
2012-06-20 6/19/12: LCD Board layout complete with desired LCD footprint. DXF file updated.
    [lcd_brd.brd, lcd_brd.dxf, lcd_brd.sch]
2012-06-26 Fixed some bugs with STLPreview class caused by adding in ability to switch focus to a point other than the origin and automatically pan the camera when the STL moves depending on selected focus mode.
2012-07-09 Made some minor refactors in attempt to fix dead tab problem. Changed the methods through which different focus and mouse modes are selected through relevant enums.
    [tempTransform.stl]
2012-07-11 Added a force reload button as a temporary workaround for intermittent problems with STLPreview displays. Extracted class from Main to encapsulate WorkspaceSelecterDialog logic in a slightly less ugl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
2012-07-19 Made a few name changes that better reflect functionality. Added new OrientationIndicator as well as a new interface for listening to STLPreviewCanvas3D objects.
    [tempTransform.stl, writerTest.stl]
2012-07-27 Added a lot of the necessary bottom level functionality to allow the Workspace indicator to be generated from an STL instead of a simple set of x,y,z dimensions. There remains to be a fair amount of 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
    [testWorkspaceSTL.stl]
2012-08-01 Finished reworking to use new workspace format using STL based shape rather than simple rectangular dimensions. Extracted some STL to Shape3D functions to their own factory. Fixed some unseen bugs in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
2012-08-09 Began making some major refactors to classes that are starting to become too large. Teased out camera and transform functions from STLPreviewCanvas3D to separate classes for easier management. Good f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
2012-08-14 Added in functions to merge multiple STLObjects into one. Added function to determine what the workspace surface is and place added models on it. More redesigning and refactoring is needed to fully s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
    [testWorkspaceSTL.stl]
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2012-08-23 Moved indicator lights to STLTransformGroup and restricted scope to one model each.
    [3007.stl, tempTransform.stl]
2012-08-25 Encoder reset working
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2012-09-05 Still some bugs with collision detection after a couple changes. Added some functionality to duplicate models, remove models, reset transforms, etc. Functions are accessible through menus brought up 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
2012-09-15 Servostruder working, encoder reset was not working because ATX supply needs to be on befor talking to an encoder
    [AS5055.c, PID.c, Servo.c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]
2012-09-22 Changed names of several classes to ones that more accurately reflect the functionality. Added in ability to reorient model to rest on different faces. Added in ability to rotate model around y axis 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
    [tempTransform.stl, testWorkspaceSTL.stl]
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2012-10-12 Tested volume estimating algorithm and it seems to be working. There is a degree of error that may be due to inconsistent use of float and double precision in different parts of the code.
    [tempTransform.stl, testWorkspaceSTL.stl]
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2012-11-18 First working test print!!!
    Fixed off by one error in buffer size reporting
    Fixed the wait params in GCodeParser
    [PID.c]
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2012-12-21 No jReality yet. Major refactor to untangle the preview stuff into a better implemented MVC pattern. Divided STLPreviewCanvas3D and its supporting classes into model, view and controller packages. As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
    [tempTransform.stl]
2013-02-10 2/10/13: Revised Controller based on reworks and design changes. ~9 hours.
    [Controller Rev 2.brd, Controller Rev 2.sch, rep_ctrlr.brd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]
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2013-05-16 Fixed PID velocity
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2013-11-25 Fixed the slave select on Encoder 0
    [Servo.c, main.c]
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2014-01-17 Renamed files and folders
    Renamed the files and folder to tier final locations
    [3007.stl, Controller Rev 2.brd, Controller Rev 2.sch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]
2014-01-18 fixed servo value change lock
    I added a lock out if a sorted servo value was out of order. THis
    happened when a value was changed during the pulse cycle. I changed it
    to use a copy of the data array instead.
    [Servo.c]
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2014-01-26 stabilized the hysteresis calibration
    I removed the center re-calculation from the bounding measurement. This
    allows the upper and lower hysteresis to be different relative to the
    center.
    [PID.c, main.c]
2014-02-07 finished the calibration prcedure.
    The issue was back in the stack...
    [Servo.c, main.c]
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2014-02-28 Fixing the linker step to inlude the math library
    [KosselKinematics.c]
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2014-03-01 Ik is working (validated against the hardware)
    FK is not working correctly
    [KosselKinematics.c]
2014-03-01 yet another forward kinematics not working...
    [KosselKinematics.c]
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2014-03-17 First step of importing Bill's Inverse Velocity Kinematic calculation function. Removed typo from RBE501-2014-Delta-Kinematics.c
    Issue #14
    [KosselKinematics.c]
2014-03-17 New file to store Matlab scripts used in developing C-code and simulating results. Added script for developing Velocity Kinematics, Issue #14
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2014-03-18 Started work on implementing TODO's in 'servostock_velInverse' function, in reference to Issue #14. Major work remaining invovles forming "Forward Position Equation Derivatives" through Matlab models.
    [KosselKinematics.c]
2014-03-19 Further manipulation of TODO comments to implementation of servostock_velInverse in preparation for team meeting, in reference to Issue #14.
    [KosselKinematics.c]
2014-03-20 Issue #11
    Started 2D triangle test case
2014-03-20 Added print actions to script to get individual jacobian entries for C-code, in reference to Issue #14.
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2014-03-22 Finally got the model matching the forward kinematics, and giving reasonable velocity outputs. In reference to Issue #14.
2014-03-23 Michael DiBlasi Updated Forward Velocity Kinematics function in KosselKinematics.c from latest matlab script. Issue #14
    [KosselKinematics.c]
2014-03-25 Close #14
    I added to the README.md file the technique we are using to determine
    the Forward/Inverse Velocity of the Delta Robot. This is currently
    derived in MatlabScript.md and will be ported over to C code in the near
    future. An issue will be opened to port this technique over.
2014-04-03 Workes without the twitching
    [KosselKinematics.c, Servo.c, main.c]
2014-04-05 Michael DiBlasi - Added System Flow document. Close Issue #20, Close Issue #21.
2014-04-05 Michael DiBlasi - Added System Flow chart to SystemFlow document. Close Issue #20.
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2014-04-11 Converted Matlab script into C Code, see 'formJacobian' of 'KosselKinematics.c', and configured both forward and inverse velocity functions. Basic test cases show that forward match Matlab simulation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
    [KosselKinematics.c]
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2014-04-13 Added another Matlab generated function, 'formInvJacobian', and removed manual method for pseudo-inverse. Now both forward and inverse velocity kinematics match the test case from Matlab within a few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
    [KosselKinematics.c]
2014-04-13 Added basic test cases for velocity kinematics to verify against Matlab values. Added 'TestCases.h' to try and resolve compiler warnings. Both actions are in reference to Issue #19.
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2014-04-26 Fixed the flash overwrite bug in the flash storage
    [FlashStorageLocal.c, main.c]
2014-04-29 Added robot configuration parameters to velocity kinematics and related test cases. Added explicit parameter for angle length in elipse test case (used for maximum workspace). Updated Matlab to inclu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
    [KosselKinematics.c]
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2014-06-06 Made the encoders not work any more...
    [AS5055.c, FlashStorageLocal.c, PID.c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]
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2014-06-13 Fixing the wrap over by not reading the raw value untill its a full read.
    [AS5055.c]
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2014-07-08 fixed the joint vector override
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2014-08-19 Fixing the packed structs
    [PID.c]
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2014-08-20 Better error printouts
2014-08-21 Fixed the offset of the variables to the fixed point scaling
    [main.c]
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2014-09-06 added steinhart-hart RTD approximation equations and tested the hot end by heating and cooling it manualy. The PID controller still won't drive the output pin of the fets. kevin suggested this is a c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
    [ForgeHeater.c, main.c]
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2014-09-07 Tweaks to test broken stack
    [ForgeHeater.c, main.c]
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2014-09-07 Fixing all of the rest of the IO manipulations
    [ForgeHeater.c]
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2014-09-07 Fixed teh Rev4 definitions
    [ServoStock.h]
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2014-09-10 Fixed the slicer packet size
    [AS5055.c, FlashStorageLocal.c, PID.c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]
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2014-10-31 Inline array definition seem to not work at all
    I switched the inline array definition back to the static memory. This
    makes the memory footprint much bigger, but it is nessissary.
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

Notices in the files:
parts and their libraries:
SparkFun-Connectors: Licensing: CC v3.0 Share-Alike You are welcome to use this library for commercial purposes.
